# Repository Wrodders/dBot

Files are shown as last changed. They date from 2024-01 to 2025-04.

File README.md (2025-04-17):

# Two Wheel Self Balancing Mobile Robot

Final Year Capstone Mechatronics Project. 
Designed to be a cost effective platform for research and development of autonomous 
mobile robotics. The non linear and unstable dynamics of the Two Wheel Self Balancing Mobile Robot (TWSBMR)
make it a challenging platform for control and navigation.

Low Level motor control implemented on STM32F411RE microcontroller, using LibOpenCM3.
High Level Monocular Navigation uses RaspberryPi 5 with the Pi Camera V3.
[ComsTerm](https://github.com/Wrodders/ComsTerm) used as engineering UI. 

## Design
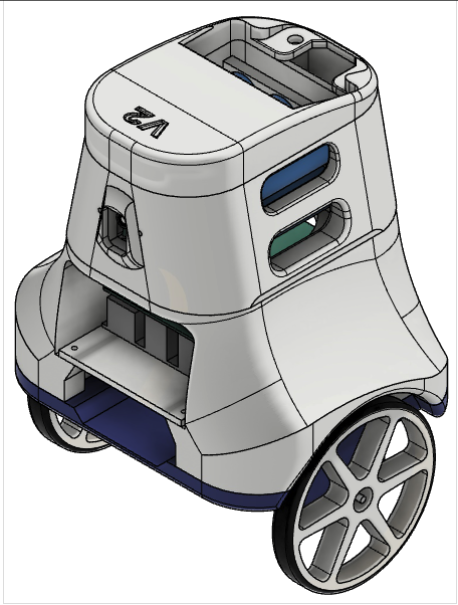
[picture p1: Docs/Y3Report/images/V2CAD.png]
botISO


The project was built around milestones of autonomy:

* Stabilization
* Positional Control
* Teleoperation
* Path Following 
* Path Recovery 
* Track Racing

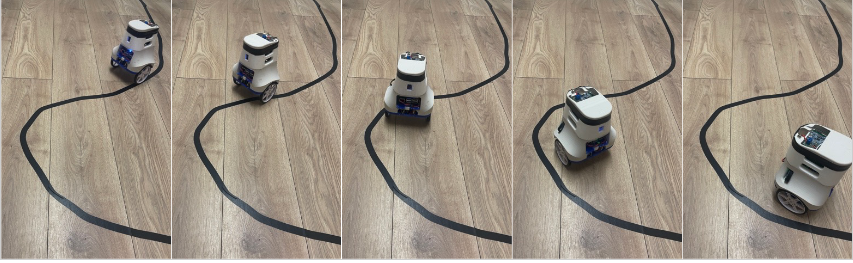
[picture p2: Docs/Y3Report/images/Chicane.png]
CurveSequence


Cascaded_Controller

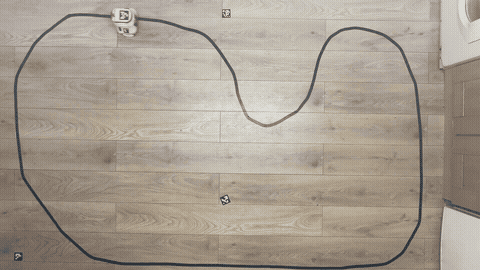
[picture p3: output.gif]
Video


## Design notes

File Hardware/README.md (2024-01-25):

# STM32 Black Pill Connection Diagram

```mermaid
graph TB
  subgraph STM32F401
    USART2 -->|PA2/3| Debug/Prog
    USART1 -->|PB6/7| Bluetooth
    TIMER3 -->|PA6/7 PB0/1| PWM
    TIMER1 -->|PA8/9/10/11| Encoder
    I2C1 --> |PB8/9| MPU6050
  end
```

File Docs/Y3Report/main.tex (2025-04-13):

%%%%%%%%%%%%%%%%%% USAGE INSTRUCTIONS %%%%%%%%%%%%%%%%%%
% - Compile using LuaLaTeX and biber, unless there is a particular reason not to. Do not use the older LaTex/PDFLaTeX or BibTeX. (The fonts won't work correctly.)
% - Font and the report 'year' must be specified when all \documentclass or the template won't work correctly. (There's no error checking/default cases!)
% - For best performance save images/graphics as PDF files, not as png/jpg/eps. This makes no difference to how images are inserted using \includegraphics.
% - As many further packages as wanted can be loaded. Below are just an example set. Note that template itself loads a number of packages, including hyperref.
% - References are handed using biblatex.
% - Link to the presentation of theses policy: https://documents.manchester.ac.uk/DocuInfo.aspx?DocID=2863

%%%%%%%%%%%%%%%%%% META DATA SETUP %%%%%%%%%%%%%%%%%%
% This is where the document title and author are set. Other details for the title page are set later
% Note that if/when you edit these you may need to 'Recompile from scratch' to get the changes to display in the PDF. (In Overleaf, select the down arrow to the right of the 'Recompile' button)

    \begin{filecontents*}{\jobname.xmpdata}
        \Language{en-GB}
        \Copyrighted{True}
        % More meta-data fielda can be added here if wanted, see https://ctan.org/pkg/pdfx?lang=en for fields
    \end{filecontents*}

    %%%%%%%%%%%%%%%%%% DOCUMENT SETUP %%%%%%%%%%%%%%%%%%
    \documentclass[12pt]{uom_eee_dissertation_casson} 
    %%%%%%%%%%%%%%%%%% PACKAGES AND COMMANDS %%%%%%%%%%%%%%%%%%
    % Packages
    \usepackage{graphicx,psfrag,color} % for postscript graphics files
        \graphicspath{ {./images/} }   % where to look for images
    \usepackage{amsmath}               % assumes amsmath package installed
        \allowdisplaybreaks[1]         % allow eqnarrays to break across pages
    \usepackage{amssymb}               % assumes amsmath package installed 
    \usepackage{url}                   % format hyperlinks correctly
    \usepackage{rotating}              % allow portrait figures and tables
    \usepackage{multirow}              % allows merging of rows in tables
    \usepackage{lscape}                % allows pages to be typeset in landscape mode
    \usepackage{tabularx}              % allows fixed width tables
    \usepackage{verbatim}              % enhanced version of built-in verbatim environment
    \usepackage{footnote}              % allows more control over footnote environments
    \usepackage{float}                 % allows H option on floats to force here placement
    \usepackage{booktabs}              % improve table line spacing
    \usepackage{lipsum}                % for adding dummy text here
    \usepackage[base]{babel}           % for proper hypthenation in lipsum sections
    \usepackage{subcaption}            % for multiple sub-figures in a single float
    % Add your packages here
    %\usepackage{pdfcomment}            % for alt text for accessibility
    \usepackage{booktabs}              % for better looking tables
    \usepackage[ruled,vlined]{algorithm2e}

    % Then to add images use:
    % \pdftooltip{\includegraphics[width=0.5\textwidth]{image.pdf}}{Alt-text here}
    % This makes the text in the image non-select-able though (assuming it's a vector file)
    
    % Custom commands
    \newcommand{\degree}{\ensuremath{^\circ}}
    \newcommand{\sus}[1]{$^{\mbox{\scriptsize #1}}$} % superscript in text (e.g. 1st)
    \newcommand{\sub}[1]{$_{\mbox{\scriptsize #1}}$} % subscript in text
    \newcommand{\sect}[1]{Section~\ref{#1}}
    \newcommand{\fig}[1]{Fig.~\ref{#1}}
    \newcommand{\tab}[1]{Table~\ref{#1}}
    \newcommand{\equ}[1]{(\ref{#1})}
    \newcommand{\appx}[1]{Appendix~\ref{#1}}
    %%%%%%%%%%%%%%%%%% REFERENCES SETUP %%%%%%%%%%%%%%%%%%
    % Setup your references here. Change the reference style here if wanted
    \usepackage[style=ieee,backend=biber,backref=true,hyperref=auto]{biblatex}
    % Note backref=true adds a page number (and hyperlink) to each reference so you can easily go back from the references to the main document. You may prefer backref=false if you need to stick strictly to a given reference style
    % Fixes which can't be applied in the .cls file
    \DefineBibliographyStrings{english}{backrefpage = {cited on p\adddot},  backrefpages = {cited on pp\adddot}}
    %  \renewcommand*{\bibfont}{\large}
    % Add more .bib files here if wanted
    \addbibresource{references.bib }
    
    %%%%%%%%%%%%%%%%%% START DOCUMENT %%%%%%%%%%%%%%%%%%

    \begin{document}
    \makeatletter
    \title{Design of a Two Wheel Self Balancing Line Racing Platform} % title of your thesis
    \author{Winston Scott}
    \studentid{107067151}
    \makeatother                                               
    \maketitle

    %%%%%%%%%%%%%%%%%% LISTS OF CONTENT %%%%%%%%%%%%%%%%%%
    \wordcount{9300}		                    % use \wordcount{} to set the count, \thewordcount to print in the text
    \uomtoc
    \begin{uomterms}
        \textbf{TWSB}:Two Wheel Self Balancing \\
        \textbf{DDMR}:Differential Drive Mobile Robot \\
        \textbf{LQR}:Linear Quadratic Regulator \\
        \textbf{MEMS}:Micro-Electro-Mechanical Systems \\
        \textbf{MPC}:Model Predictive Control \\
        \textbf{MCU}:Microcontroler Unit \\
        \textbf{RPC}:Remote Procedure Call \\
        \textbf{IMU}:Inertial Measurement Unit \\
        \textbf{ppr}:Pulses Per Revolution \\
        \textbf{KF}:Kalman Filter \\
    \end{uomterms}

    \uomdeclarations

    %%%%%%%%%%%%%%%%%% ABSTRACT %%%%%%%%%%%%%%%%%%
    \begin{abstract} % put abstract here. Limit is 1 page.
        The highly dynamic Two Wheel Self Balancing Robot 
        (TWSB) has a large exploration space for developing high-level 
        control strategies. 
        This report presents the design decisions and algorithms developed for
        an autonomous line-racing TWSB robot utilizing a monocular vision system with low-cost hardware. 
        System identification techniques are used to explore
        cascaded PID control strategies for the TWSB system.
        A trajectory generation algorithm is proposed based on drivability, confidence, 
        and prominence of the detected line from a camera used as an intensity sensor. 
        The performance of the system is shown to be robust to different race tracks with
        surface texture variation, lighting conditions, high-speed straights, and tight curves. 
  \end{abstract}%
  \clearpage

  %%%%%%%%%%%%%%%%%% SECTION 1 %%%%%%%%%%%%%%%%%%
    \section{Introduction}
    The Two Wheel Self Balancing (TWSB) platform is a nonlinear, underactuated system which is only dynamically stable.
    Compared to the differential drive mobile platform (DDMR), the TWSB requires active control effort
    to maintain its upright posture while in motion and when stationary.
    Substantial research has been conducted on the similarly unstable 1-DOF inverted pendulum on a cart 
    as a benchmark for control techniques \cite{boubaker2013inverted}. 
    The TWSB robot serves as a cost-effective platform for research and education in complex control 
    strategies less commonly applied to statically stable wheeled robots \cite{educationPlatform}.

    Controlling this unstable degree of freedom expands the range of autonomous behaviors that 
    can be explored \cite{RoboLimbo} \cite{jeong2008wheeled} \cite{Browning2004TurningSI}. 
    These behaviors necessitate a hierarchical design in the system's architecture,
    where planning and navigation algorithms though linked, are decoupled by levels of abstraction 
    from the low-level stability control and even lower-level motor control. This paper explores 
    the design tradeoffs at each of these levels, and the challenges with developing a robust system 
    capable of autonomous navigation in a variety of indoor environments using a monocular camera.

    A notable work on the TWSB system is \cite{grasser2002joe} which designed a TWSB robot capable of disturbance
    rejection and static pose control on an inclined plane. This was implemented using an FPGA-based DSP system.
    The controller design decouples the balancing and steering torques in state space through the Linear Quadratic Regulator (LQR), 
    allowing the platform can turn about its center effectively. This is a behavior that is fundamental to differential drive robots, 
    and accomplishing this allows for the TWSB to be navigated similarly.
    An early challenge in the navigation of the TWSB system identified by \cite{SelfContainedMobileTWSB} is the sensor 
    system used for state estimation. The proposed solution uses a gyroscope as an angular rate sensor, though it 
    was noted to suffer from drift. Accounting for this drift as a linear function over time, the authors were able to 
    stabilize the system and teleoperated it over short distances. 

    Advances in the cost-to-performance of embedded systems and micro-electromechanical sensors (MEMS) \cite{MEMS} 
    have allowed \cite{juang2013design} \cite{Velazquez2016VelocityAM} to control the TWSB system 
    using low-powered microcontrolers. This then poses the question of how to expand the capabilities 
    of the TWSB system beyond teleoperation by utilizing modern embedded computers for high-level autonomy. 
    Recent research has also applied reinforcement learning to mobile robotic systems \cite{kober2013reinforcement}.
    Neural networks are proposed as nonlinear function approximations to model the system's response. 
    These methods demonstrate robustness to un-modeled or neglected dynamics \cite{guo2021optimal}.

    In mobile robotics, the ability to navigate requires perception. LIDARs are commonly used, as  
    the depth of information they capture naturally lends itself to path-planning algorithms.
    Another commonly used multimodal sensor is the CMOS camera, which measures light intensity at each pixel. 
    When paired in stereo, it can efficiently infer depth, providing a suitable alternative to the point 
    clouds generated by LIDAR. Although monocular vision systems are desirable due to their simplicity, 
    the redundancy of stereo vision is beneficial in safety-critical applications.
    Both these sensors provide rich environmental data that can be leveraged to develop long-term path-planning algorithms \cite{gonzalez2015review}.

    This paper is split into 2 parts, the first part focuses on the design of the TWSB system, and the second part
    develops a vision-based line-following algorithm, geared towards racing applications. By exploring 
    the performance of the TWSB at its handling limits, this project tests the viability of the designed robot
    as a platform for further research on wheel robotic navigation. 

    Autonomy is achieved using a hierarchical cascaded PID feedback controller. This aims 
    to regulate the pitch angle maintaining balance when controlling the robot's linear velocity. 
    Once these requirements are met, the robot can be teleoperated intuitively via a 
    smartphone-based web interface. The remainder of this paper focuses on incorporating 
    multimodal sensor data from the camera to develop line-racing algorithms.
    The robot algorithmically infers and follows an unknown line using a monocular camera. 
    A hardware-in-the-loop software architecture is implemented, enabling real-time telemetry data and control 
    commands to be exchanged between the robot and a remote computer, but all computations are performed onboard. 
    Visualization of this telemetry data provides a straightforward means of validating the robot's performance.

  %%%%%%%%%%%%%%%%%% SECTION 2 %%%%%%%%%%%%%%%%%%
    \section{Mathematical Modeling} % edit section heading as appropriate
    In this report, the TWSB decomposed into 2 commonly studied 2DOF subsystems, described by Fig.\ref{fig:2DOF}, and their behavior is analyzed
    separately.
    Effective control and planning algorithms for such platforms require the designer to obtain a mathematical model describing the behavior
    of the robot.  
    For the TWSB system, these models are commonly obtained by a linear approximation of the dynamics similar to 
    of the classic inverted pendulum \cite{AdvancedWIP}.
        \begin{figure}[h]
            \centering
            \begin{subfigure}[b]{0.4\textwidth}
                
                \caption{Differential Drive Mobile Robot}
                \label{fig:DDMR}
            \end{subfigure}
            \hfill
            \begin{subfigure}[b]{0.4\textwidth}
                
                \caption{Wheeled Inverted Pendulum}
                \label{fig:WIP}
            \end{subfigure}        
            \caption{Robot subsystems}
            \label{fig:2DOF}
        \end{figure}

        \subsubsection{Differential Drive Mobile Robot}
    Wheeled mobile robots are typically restricted to navigation in the 2D Cartesian plane. For small robots 
    this configuration, motion models are often simplified by discounting the nonlinear dynamics of friction and 
    the inertial forces arising from acceleration in the $X'$ direction are negligible \cite{KinematicWheeled}. 

    The DDMR's nonlinear kinematics are obtained from Fig.\ref{fig:DDMR} describe point $G=(x_g,y_g)$ as the position of 
    the robot in the global frame.
        \begin{equation}
            \begin{bmatrix}
                \dot x_g \\
                \dot y_g \\
                \dot \psi
            \end{bmatrix}
    =
            \begin{bmatrix}
                \cos(\psi) & 0 \\
                \sin(\psi) & 0 \\
                0 & 1
            \end{bmatrix}
            \begin{bmatrix}
    v_g \\
                \omega_g
            \end{bmatrix}
            \label{eq:DDMRGlobal}
        \end{equation}

    Where the angular velocity $\omega_g$ and linear velocity $v_g$ are the control 
    inputs to the system. 

    The motion of the DDMR is bounded by its non-holonomic constraints, 
    preventing lateral movement along the $Y'$ axis. 
    Under the pure rolling assumption, the wheels do not slip, and the robot's kinematics 
    are governed by the wheel radius $r$ and wheelbase $d$. These parameters define 
    the mapping between the left and right wheel velocities, $\omega_L$ and $\omega_R$, 
    and the global velocities $v_g$ and $\omega_g$, by:
        \begin{equation}
            \begin{bmatrix}
    v_g \\
                \omega_g
            \end{bmatrix}
    =
            \begin{bmatrix}
                \frac{r}{2} & \frac{r}{2} \\
                \frac{r}{d} & -\frac{r}{d}
            \end{bmatrix}
            \begin{bmatrix}
                \omega_L \\
                \omega_R
            \end{bmatrix}
            \label{eq:DDMR}
        \end{equation}

        \subsection{DC Motor Model}    
    The robot is driven by two DC motors, through planetary gearboxes, as shown in Fig.~\ref{fig:DCMotor}.
    When a voltage $V_a$ is applied, the DC motor generates a torque, $\tau$, 
    proportional to the armature current, $i_a$.
    According to Lenz's law, the back electromotive force (emf), $e_a(t)$, 
    opposes the applied voltage. These relations are given by:
        \begin{subequations}
            \begin{align}
                \tau &= K_t i_a \\
    e_a &= K_e \dot{\phi}_r
            \end{align}
        \end{subequations}
    where $\dot{\phi}_r$ represents the rotor's angular velocity. The torque 
    and back emf constants are denoted as $K_t$ and $K_e$, respectively.
        \begin{figure}[H]
            \centering
                
            \caption{Gearbox DC Motor Model Diagram}
            \label{fig:DCMotor}
        \end{figure}
    In small motors, since $L_a \ll R_a$, the electrical dynamics can be approximated as:
        \begin{equation}
    i_a (t) = \frac{V_a (t) - K_e \dot{\phi}_r (t)}{R_a}
        \end{equation}

    The rotor torque, $\tau_r$, is transmitted through the gearbox, which 
    reduces the angular velocity of the wheel, $\dot{\phi}_w$, by the gear ratio $n = \frac{N_2}{N_1}$. 
    Assuming the gearbox is lossless the wheel torque, $\tau_w$, is given by:
        \begin{equation}
                \tau_w = n\tau_r
        \end{equation}
    where $N_1$ and $N_2$ are the number of teeth on the input and output gears, respectively.
    The rotor's inertia $J_r$ and the drive train damping, $B_r$ and $B_g$, are also considered negligible.
    By summing the torques of the rotor and gearbox subsystems, the output torque is given as:
        \begin{equation}
            \tau_w = - J_g \ddot{\phi}_w - \dot{\phi}_w \left( \frac{K_t K_e}{R_a} n^2 \right) + \frac{n K_t V_a}{R_a}
            \label{eq:DCMotorTorque}
        \end{equation}
    where $J_g$ represents the gearbox's inertia and $B_g$ its damping coefficient.

        \subsection{Wheeled Inverted Pendulum}
    The wheel inverted pendulum (WIP), is similar to the classic inverted pendulum on a cart. 
    The WIP is composed of 2 rigid bodies, the body and the chassis connected by a revolute joint, 
    at the center of mass of the wheel as shown in Fig.\ref{fig:WIP}. 
    The center of mass of the body, $B=(x_b,z_b)$, 
    is located at a distance $L$ from the wheel's axel, displaced at some pitch angle $\theta$ with 
    the vertical axis $Z$. The body is assumed to be a point mass $M_b$ with a moment of inertia $J_b$ 
    about the axis of rotation. 
        
    The system of equations governing the time evolution of the WIP are well known.
        \cite{frankovsky2017modeling} \cite{ModelingWIPLagrange}.
    This paper uses the 2DOF state space model as obtained by \cite{Velazquez2016VelocityAM} since it describes 
    the hardware of a similar configuration to the TWSB designed in this project. 
    Incorporating the torque produced by each actuator, eq(\ref{eq:DCMotorTorque}),
    and reiterating the no-slip condition 
        \begin{equation}
            \phi_w = \frac{x}{r}
        \end{equation}
    the model is re-expressed in the notation of this report as 
        \begin{equation}
            \begin{bmatrix}
            \dot{x} \\
            \ddot{x} \\
            \dot{\theta} \\
            \ddot{\theta} 
            \end{bmatrix} =
            \begin{bmatrix}
            0 & 0 & 0 & 0\\
            0 & \frac{2n^2 K_t K_e }{r^2 R_a W_1 } & \frac{-M_b^2 L^2 g}{W_1 \left(J_b +M_b L^2 \right)} & 0\\
            0 & 0 & 0 & 1\\
            0 & \frac{2n^2 K_t K_e }{r^2 R_a W_2 } & \frac{-M_b^2 L^2 g}{W_2 \left(\left(J_b +M_b L^2 \right)+W_1 g\right)} & 0
            \end{bmatrix}
            \begin{bmatrix}
    x\\
            \dot{x} \\
            \theta \\
            \dot{\theta} 
            \end{bmatrix} +
            \begin{bmatrix}
            0\\
            -2n\frac{K_t }{W_1 R_a r}\\
            0\\
            -2n\;\frac{K_t }{W_2 R_a r}
            \end{bmatrix}
    V_a
        \label{eq:2DOF}
        \end{equation}

    with 
        \[
    W_1 = 2\left(\frac{-n^2 J_g + J_w }{r^2 } - M_w \right) - M_b + \frac{M_b^2 L^2 }{J_b + M_b L^2 }
        \]
        \[
    W_2 = W_1 \left(\frac{J_b }{M_b L} + L\right)
        \]

    Where $M_w$ is the mass of the wheel, $J_w$ is the moment of inertia of the wheel.
    \pagebreak{}

    \section{System Design}
        The robot must be designed to approximate the wheel-inverted pendulum system, many authors 
        construct demonstrators supporting a mass with a rectangular structure built out of lead screws. 
        This allows for experimentation with the system's center of mass and is simple to construct. 
        A proof of concept system was developed in this manner, however, the exposed electronics were 
        susceptible to damage during tuning of the balance and navigation algorithms.

        As such the TWSB body is 3D printed out of PLA plastic in 3 parts for minimal assembly.
        The battery pack is quickly swappable and both it and the electronics sub-assembly 
        are soft-mounted in a roll cage-like housing for protection against impacts. 
        The wheels are protected by wheel arches which serve to minimize risk of damage to the motor shaft on wheel impacts. 
        Wiring harnesses are routed through channels to minimize snagging and disconnection from vibrations.
        
        \begin{figure}[H]
            
            \caption{CAD Drawing of the TWSB system dimensions in mm}
            \label{fig:CAD}
        \end{figure}

        Two brushed DC motors are powered by an H-Bridge IC, DRV7783. 
        The STM32F411RE Microcontroller Unit (MCU) is used to control the 
        motors and monitor the 6 6-axis inertial Measurement Unit (IMU) over I2C. It communicates with the 
        Raspberry Pi 5 over UART via a custom ASCII protocol discussed in section 3.1. 
        The system is powered by a 12V nominal Li-ion Battery pack. A USB-C CC-CV charger is used for quick 
        and accessible recharging, critical for mobile robotics applications. 
        Battery voltage is monitored by the MCU and the pack is protected by a BMS.
        A simple circuit adapted from \cite{chu2008designing} is used to safely load share between the battery pack and the charger.

        \subsection{Software Architecture}
        The modern standard for robotics software is the Robot Operating System 2 (ROS2) \cite{Macenski2022RobotOS}. 
        It is composed of several highly configurable applications that are designed to be managed in a distributed system.
        Distributed systems are beneficial in robotics development as they functionally decouple the software components, 
        enabling robust failure recovery and ease of integrating new features. This concept is useful for this project as 
        the core control and vision systems are developed in parallel. The controls, logs, and error recovery systems mandate 
        high availability compared to user interfaces such as the remote control web app. 
        Whilst this is a powerful tool, it is deemed too complex to learn to meet the project deadline.
        Nevertheless, some core concepts are used such as sharing state by message passing between components, 
        and dynamic parameter configuration to improve testing and data collection. The ZeroMQ middleware is used for 
        timestamped signal stream communication between the computational nodes. 
       
        The software, written in C++, is managed by Systemd as a service. 
        Self-diagnosis routines are used for resource monitoring and auto-recovery. 
        Programs operate on runtime parameters through Remote Procedure Calls (RPC) 
        interface using a GET-SET pattern. This reduces the 
        compile flash debug iteration time. A GStreamer pipeline sets up a video 
        server accessible over LAN. OpenCV is used for optimized image processing.
             
        The firmware is implemented in C using register definitions from the 
        libopencm3 project \cite{BeginningSTM32} as an exercise in low-level programming. 
        No dynamic memory allocation is used.
        The resultant binary is 19KB with 892B of RAM used.
              
        The data-acquisition system obtains a timestamped sample of the 
        telemetry values transmitted by the MCU through a serial link, which implements the
        RPC interface over uart at 230400 baud, 
        it executes commands and publishes telemetry packets at 100Hz.
        Parsing the UART IO buffer can result in non-uniformly sampled data as it
        is constrained by the OS scheduler, thus an event-driven system is used to 
        minimize CPU overhead.
               \subsubsection{Parameters }
        The system parameters are given in Table \ref(tab:SysParams). 
        The mass of the sub-components is obtained by weighing,
        and estimates of the 3D printed parts' mass are given by the slicer software. 
        The CAD files are used in MATLAB's Multibody Simulink environment, which 
        computes the center of mass and the moments of inertia can subsequently be estimated.
        The Motor parameters are estimated through the system identification experiments discussed in section 3.2.
                    
        \begin{table} [H]
            \centering
            \begin{tabular}{|c|c|c|c|}
                \hline
                Parameter & Value & Units & Description \\
                \hline
                $M_b$ & 0.8 & kg & Mass of the body \\
                $L$ & 0.08135 & m & Height of COM above wheel axel \\
                $J_b$ & 0.0071& kgm$^2$ & Moment of inertia of the body \\
                $r$ & 0.04 & m & Radius of the wheel \\
                $M_w$ & 0.09 & kg & Mass of wheel assembly \\
                $J_w$ & 0.000072 & kgm$^2$ & Moment of inertia of the wheel \\
                $d$ & 0.132 & m & Wheel base \\
                $R_a$ & 1.5 & $\Omega$ & Resistance of the motor \\
                $K_t$ & 0.24 & Nm/A & Torque constant of the motor \\
                $K_e$ & 0.18 & V/rad/s & Back EMF constant of the motor \\
                $n$ & 20 & - & Gear ratio \\
                $J_g$ & 0.0003 & kgm$^2$ & Moment of inertia of the gearbox \\
                \hline
            \end{tabular}
            \caption{System Parameters}
            \label{tab:SysParams}
        \end{table}

        \subsection{System Identification}
        A set of experiments are conducted to evaluate the transfer function of the motors.

        \begin{table}[H]
            \centering
                \begin{tabular}{|r|c|c|c|c|c|c|}
                    \hline 
                    Gear Ratio & Rated Torque & Rated Speed  & Rated Current & Stall Current & Stall Torque \\
                    \hline
                     1:20  & 0.39 Nm & 600 rpm & 500 mA & 2 A & 0.15 Nm/Kg \\
                    \hline
                \end{tabular}
                \caption{Manufacturer Provided Motor Parameters}
        \end{table}

        A telemetry and analysis software system developed in Python. It is used as 
        test bench  setup shown in Fig.\ref{fig:SysIDSetUp}, a series of reference 
        ramp, step, sine, and chirp inputs are applied to each motor.

        The test suite contains a time-series signal generator, with preview and playback functionality.
        The system logs and messages are displayed in a terminal window, and the user can fully configure 
        each node's runtime parameters remotely over a network connection, utilizing the RPC ASCII protocol.
        A line plotter is configured by JSON to display any number of signals the robot may produce.
        This architecture allows for repeatability in obtaining robot data, something 
        is is a challenge in mobile robotics.
        
        \begin{figure}[H]
            \centering
            
            \caption{System Identification Testbench Setup}
            \label{fig:SysIDSetUp}
        \end{figure}
      
        This software system is also utilized for heuristic tuning of the control
        and vision systems. The program can visualize control signal streams in soft real-time 
        and provides a useful insight into the effects of the control system on the plant.

        \begin{figure}[H]
            \centering
            \begin{subfigure}[b]{0.45\textwidth}
            
            \caption{Open Loop Step Response}
            \label{fig:openstep}
            \end{subfigure}
            \hfill
            \begin{subfigure}[b]{0.45\textwidth}
            
            \caption{Open Loop Sine Response}
            \label{fig:opensine}
            \end{subfigure}
            \caption{Open Loop no Load Speed Voltage Experiments}
            \label{fig:openloop}
        \end{figure}

        From these experiments, it is clear that the motor has significant deadzones, 
        and the input-output relationship is nonlinear at low armature voltages. 
        The maximum no-load speed within the manufacturer's operating range is found to be 8 rotations per second.
        To increase control authority, the motors are powered by 12V, with the armature voltage modulated by 
        the duty cycle of the PWM signal. The DRV7783 Integrates current sensing and over-current protection,
        used to limit the current to the motors to 1.5A.
              
        For stationary balancing of the TWSB robot
        the actuators are required to operate mostly in a sinusoidal fashion, 
        similar to Fig.\ref{fig:opensine}, to regulate the pitch angle of the body.
        Considering this a closed-loop controller is developed in section 5.1 to regulate the motor speed,
        and maintain the device in its operating region. 
       
           \section{State Estimation}
        Information about the TWSB system may be obtained from 2 kinds of sources; 
        mathematical models models as in eq(\ref{eq:2DOF}) which can describe the time evolution of the chosen system variables, 
        and sensors that convert energy arising from a physical property into information. Both of these sources 
        are approximations of the true state. The process of combining multiple sources of information is termed sensor fusion.
        This section evaluates the available methods employed using \textit{proprioceptive} sensors.
           \subsection{Sensors Overview}
        For the TWSB system in eq(\ref{eq:2DOF}) its state variables $\theta$ and $\dot x_b$ can be measured through the onboard IMU 
        and the wheel encoders respectively. 
                   
        The motors incorporate a low-cost 12 pulses per revolution (PPR) incremental encoder on the rotor shaft. 
        Further resolution is easily obtained by using the MCU's quadrature 
        peripheral to increment, or decrement, a counter based on the phase transitions.
        Considering the gearbox ratio $n=20$, an effective resolution of 960 PPR is attained.
        The rotational speed of the wheel is computed by sampling the change in the pulse counts
        over a sample period $\Delta t$. Thus the error in the velocity estimate, 
        is inversely proportional sample period, resulting in larger errors at low speeds.
        Yet, it is observed that more significant sources of error arise from the mechanical backlash in the gearbox.
        The sample time is set to 2 ms, and a low-pass filter is given by the infinite recursive relation as
        \begin{equation}
            y_k = \alpha x_k + (1-\alpha)y_{k-1}
            \label{eq:lpf}
        \end{equation}
        exponentially attenuates sudden deviations in the velocity estimate by selecting $\alpha = 0.95$.
       
        Using this velocity estimate in the model of the DDMR from eq(\ref{eq:DDMRGlobal}) to obtain the
        position of the robot in the cartesian plane as ($x_g,y_g$) is known as odometry.
        There are various sources of errors in 
        this process, arising from assembly imperfections and conditions in 
        the environment which may break the constraints assumed in the kinematics of the DDMR.
                   
        These conditions become significant in the case of the TWSB system as crashes, or bumps, result in large 
        and unbounded error accumulation. In the case of crashes, the robot is subsequently stationary 
        and its state is reset. However, in the case of bumps, where the robot can recover, corrective 
        action is required to mitigate this. Assuming a sufficiently accurate wheel encoder, a simple method is 
        implemented based on \cite{Gyrodometry}, only correcting 
        the odometry when such events are detected.  
        This leads to the decision that other forms of systematic odometry errors have to be 
        either disregarded in the short term or corrected by landmark methods by $exteroceptive$ sensors. 
       
        The IMU is a 6-axis MEMS sensor \cite{ComplimentaryKalman} which measures the local linear acceleration 
        and angular velocity.
        The 3D acceleration, $\vec{a}$, is used to obtain an 
        estimate of the pitch angle as $\hat{\theta} = \mathrm{atan2}\left(-a_x ,a_z \right)$
       
        The variance of this $\hat{\theta}$ is small when the system is at rest but grows larger when subject to vibration from the motors
        as shown by the experiment in Fig.\ref{fig:accelNoise} where the TWSB is placed horizontally at rest and motor control commands are issued. 
        \begin{figure}[H]
            \centering
            \begin{subfigure}[b]{0.5\textwidth}

                
                \caption{Accelerometer is sensitive to motor vibrations}
                \label{fig:accelRaw}
                
            \end{subfigure}
            \hfill
            \begin{subfigure}[b]{0.45\textwidth}
                
                \caption{Wide Variance on pitch estimate at rest}
                \label{fig:pitchNoise}
            \end{subfigure}
            \caption{Accelerometer Noise}   
            \label{fig:accelNoise}
        \end{figure}

        From \ref{fig:pitchNoise} it can be seen that the IMU is not mounted perfectly orthogonal to the body frame. 
        \begin{table}[H]
            \centering
            \begin{tabular}{c c c} 
                \toprule
                $a_{x_0}$ & $a_{y_0}$ & $a_{z_0}$ \\
                \midrule
                0.036453 & -0.0021066 & 0.133658 \\
                \bottomrule

            \end{tabular}
            \caption{Accelerometer Mounting Offset (m/s$^{2}$)}
            \label{tab:accelOffset}
        \end{table}
        This systematic error is removed by utilizing calibrated values in Table \ref{tab:accelOffset}.
        \subsection{Kalman Filter}
        The Kalman Filter (KF) and its variants  are widely used in robotics to fuse 
        complementary sources of information \cite{Thrun2005ProbabilisticRobotics} \cite{perez2023quadcopter} \cite{Moore2014AGE}.
        Even though the state transition model of the TWSB robot is non-linear \cite{ooi2003balancing} 
        developed self-balancing platforms capable of restricting oscillations about the 
        operating point to $±1$ degree. This is one order of magnitude than the worst-case linearization pitch limit of $±10$ degrees.
        Beyond this, the small angle approximation is no longer valid, and the system is not locally linear. As such it is determined 
        that if the controller is able to regulate the pitch to within this range, then the optimum linear estimator known as the Kalman Filter is suitable.

        The Kalman Filter is a 2-stage recursive estimator which uses the system model to predict the state of the system,
        and then corrects this prediction using the measurements from the sensors. The notion of a prediction and correction 
        stems from Bayesian statistics, where signals are modeled as random variables with a probability distribution.
        The Kalman Filter is applicable to linear systems, and as such the random variables are assumed to be normally distributed. 
        Considering a linear stochastic system of the form:

        \begin{equation}
            x_t = A_t x_{t-1} + B_t u_t + \epsilon_t
        \end{equation}

        where $\epsilon_t$ is a noise term with zero mean and covariance $Q_t$. The Kalman Filter is concerned with 
        updating its posterior belief in the true state of \textit{bel}$(x_t)$ with some weighted sum of the 
        information from the prior belief \textit{$\bar{\text{bel}}(x_t)$}, the current measurement $z_t$, and the evolution of 
        the model of the system through the control action $u_t$.

        At each time step $t$, the TWSB system obtains new measurements from its sensors, which are related to the state space by:

        \begin{equation}
            z_t = C_t x_t + \delta_t
        \end{equation}

        where $\delta_t$ is a noise term with zero mean and covariance $R_t$.  
        Often noise variables of this kind are denoted as part of the $N(0, R_t)$ group of random variables.
        The matrix $C_t$ maps the measurements to the state space as a linear transformation.

        Before the measurement can be used, the Kalman Filter must first obtain an estimate of the state given the 
        prior belief and the control action. This is termed the prediction stage, where the current mean, given the prior mean, 
        is predicted through applying the current control action to the system model. This prediction increases the uncertainty of the belief through the 
        process noise, which is a random variable given as $N(0, Q_t)$. This process noise is assumed to be independent from the measurement noise.
        The prediction step is given by the equations:

        \begin{equation}
            \mu_{t|t-1} = A_t \mu_{t-1|t-1} + B_t u_t
        \end{equation}
        \begin{equation}
            P_{t|t-1} = A_t P_{t-1|t-1} A_t^T + Q_t
        \end{equation}

        By the linearity of Gaussian distributions, incorporating the measurement will reduce the uncertainty in the posterior belief. 
        This is done through the Kalman Gain matrix as:

        \begin{equation}
            K_t = P_{t|t-1} C_t^T (C_t P_{t|t-1} C_t^T + R_t)^{-1}
        \end{equation}
        \begin{equation}
            \mu_{t|t} = \mu_{t|t-1} + K_t (z_t - C_t \mu_{t|t-1})
        \end{equation}
        \begin{equation}
            P_{t|t} = (I - K_t C_t) P_{t|t-1}
        \end{equation}

        The state transition model used by the KF can be chosen to model the TWSB system eq(\ref{eq:2DOF}) as a step towards 
        full state feedback, or solely based the dynamics of the IMU.
            
        The MPU6050 6-Axis IMU can be used to  estimate the pitch through the 
        gyroscope measurement $\vec\omega_{gyro}$, which due to its mass spring construction, even if miniutrazizred, suffers from a drift noise term. 

        \begin{equation}
            \vec\omega_{gyro} = \omega + b_g + n_g
        \end{equation}

        and the accelerometer measurement \ensuremath{\vec{\alpha}_{accel}} is from as 
        
        \begin{equation}
            \vec{\alpha}_{accel} = \alpha - g + b_a + n_a
        \end{equation}
        Where the external acceleration arising form linear motion is given as $\alpha$, accelerometers bias by $b_a$ and noise by $n_a$. 

        A Kalman Estimator is developed to fuse the gyroscope and accelerometer measurements, using the model of the IMU obtained similar to \cite{ComplimentaryKalman}.
        This is implemented on the microcontroler at 1Khz.  

        \begin{figure}[H]
            \centering
            
            \caption{Sensor Fusion of accelerometer and gyroscope}
            \label{fig:SensorFusion}
        \end{figure}
             
        Fig.\ref{fig:SensorFusion} shows that the Kalman Filter's produces a smooth estimate of the pitch angle
        under conditions of the experiment in Fig.\ref{fig:accelNoise}. 
        \pagebreak{}

    \section{Control System}
        Autonomy in mobile robotics is commonly a hierarchical problem composed of high-level path planning, 
        or task allocation, and low-level control of the actuators.  
        Successful implementations must design solutions to both of these problems in a complementary manner in order 
        to achieve the desired system behavior, of tracking the planned configurations.
                
        For the TWSB robot, behavior can be described by two main goals, static balancing and navigation.
        These two behaviors are inherently coupled due to the system's underactuated design. Hence, the 
        magnitude of the feedback required for sufficiently fast stabilization leads to significant chatter or oscillations 
        in the control signal.
    
        Gain scheduling is suggested by \cite{refvem2019design}
        as a way to operate the system in these two different modes. A similarly underactuated system is controlled via this 
        method by \cite{wanggain}. Notably, in these cases care must be taken to ensure 
        that discontinuities in the control signal at the point of switching do not cause instability \cite{hespanha2002switching}.
        Determining the switching schedule is a nontrivial problem, often mandating experimental validation-dependent 
        on the systems parameters, \cite{RoboLimbo} utilizes advanced nonlinear strategies to determine these
        boundary conditions.
    
        The tracking performance of reactive control strategies is often bounded by the control effort 
        demanded within the bandwidth of the actuators. Typically in feedback systems, a saturation function 
        is utilized on the reference to enforce safe operation. This discontinuity breaks the linearity of the 
        controller often leading to oscillations, and care must be taken to avoid such limit cycles.
                
        The PID regulator is an attractive choice for many systems, as by nature of negative feedback it does not 
        require an explicit model of the plant to operate. The process variable is typically a direct measurement 
        obtained by a sensor, and the control law $u_k$ is computed reactively to an error signal at each timestamp $k$.
        Oftentimes, intuition about the signal's physical units is sufficient to tune the feedback gains adequately. 
        However, performance validation in the model-free case must be evaluated at runtime, this may prove to be 
        challenging or destructive in cases of unstable or safety-critical systems. 
            
        Heuristic methods such as Ziegler-Nichols formulate approaches to black-box tuning of a plant by observing the system 
        performance under sustained instability and designers experimentally tune such algorithms.
        For example, from the input-output data of the selected actuators obtained in Fig.\ref{fig:openloop}, 
        it can be seen that a large integral action is needed to overcome the steady-state error.
        This is a common issue in low-cost DC motors, where the static friction of the gearbox presents 
        a nonlinearity which is most notable at low control authority and difficult to model. 
        
        Model-based control allows the designer to validate the performance of the system in simulation. 
        Often frequency domain tools are used to analyze the plant in an open loop. From this, a control law is designed around 
        the controllable state variables with physical information on the behavior of the system.
        Given a model of the system, designers also can formulate constraints, 
        and obtain an optimal control signal which meets these. For example, by minimizing the control effort in a cost function
        the challenges associated with choosing a saturation safety function can be mitigated.
        
        Parameter uncertainty is a common issue in controlling mobile robotics, and approximations of these often lead to 
        discrepancies between the mathematical optimal solutions found in simulation \cite{eide2011lqg} 
        and in real world performance \cite{tran2023fuzzy}. The difficulty with purely model-based approaches is
        the need for a high-fidelity model and access to low-uncertainty measurements of the state variables.
        
        A model of a TWSB robot, incorporating the non-idealities of low-cost DC motors is proposed by \cite{yamamoto2008nxtway}.
        It is used together with a simulation study of a WIP platform as a reference solution for the TWSB problem.
    
        Another approach is to use actuators with more favorable characteristics for the task at hand, such as stepper motors.
        The static balancing problem aims to control $\theta$ and regulate the linear displacement. The coupling of the 
        pitch angle to the rate of change in linear position requires active control, resulting in oscillations in both these state variables. 
        Stepper motors draw a nominal current, thus maintaining high torque at low speeds, eliminating the need for gearboxes and the 
        backlash associated with them. 
                
        The field of adaptive control proposes dealing with system uncertainties by designing controllers that may 
        learn over time. Online trial-and-error data and statistical techniques like regression-based transfer
        function estimation from input-output data are used to develop physics-informed models taken under statistical 
        distributions of belief \cite{benosman2018model}.         
                    
        In a similar vein, \cite{williams2016aggressive} embeds a neural network as an online function approximator to learn 
        predictions of the dynamics of the system. This prediction is then used as part of a trajectory planner in race-line optimization. 
        Some modern microcontrollers have sufficient computational power requirements needed for Model Predictive Control (MPC) and 
        effective implementations of convex optimizers \cite{nguyen2024tinympc} have been used in small mobile robots \cite{giernacki2017crazyflie}.
                
        An attractive aspect of predictive approaches to control is that they lend themselves naturally to 
        planning long horizons. These methods use numerical simulation techniques to evolve the system over time 
        and estimate the distribution of state probabilities through sampling of control actions. 
        The optimal control sequence is then chosen from these samples using a cost function.
                    
        The autonomous behavior of the TWSB robot explored in this paper is that of the path 
        following in an unknown environment, where no prior map is available. As such the 
        the control system has three goals, namely disturbance rejection of the pitch angle; 
        this is required such that the system is robust to the environment, minimizing 
        the linear displacement when stationary and tracking a trajectory obtained by a 
        high-level planner discussed in section 6. 
    
        A simple PID controller operating on the pitch error is tested in a simscape multibody; 
        a physics-based simulation where the control law is an applied force to a prismatic joint. 
        This force is coupled through the revolute joint to the pitch angle as described by \ref{eq:2DOF}.
        This manages to stabilize the pitch angle yet the $x$ position drifts over time as this 
        state variable is not controlled.
        More complete control laws are discussed in the following sections.
        \subsubsection{Controler requirements}

        The TWSB achieves balance by controlling the oscillations of the pitch angle about the 
        vertical axis. The linear system of equations in eq.(\ref{eq:2DOF}) is applicable 
        only when the pitch angle is small, this is taken to be $\theta < ±10$ degrees. 

        The advanced non-linear control methods discussed above are beyond the scope of this project. 
        Whilst their performance guarantees under real-world conditions are attractive, it is often simpler 
        to implement complex behaviors in the high-level planner.
        In the sequence, the low-level controls are developed to meet these requirements:
        \begin{enumerate}
            \item The pitch angle must be regulated to $±1$ degree.
            \item The robot must be able to safely recover from disturbances due to external forces and the environment.
            \item The robot must be able to track a reference velocity, with minimum overshoot.
        \end{enumerate}

        \subsection{Cascade PID}
                
        In the planer case shown in Fig.\ref{fig:WIP} the trajectory of the center of mass is parametrized by 
        the pitch angle $\theta$ and the linear velocity $v_b$. 
            
        A cascaded PID controller is used to control the pitch angle and the linear velocity. 
        Control of the position $(x_g,y_g)$ is left to a higher-level planner.  
        If the inner loop dynamics are much faster than the outer loop, 
        then the inner loop can be approximated as a disturbance \cite{Robust2DofPID}.

        Again, simscape multibody is used to verify the feasibility of this kind of controller Fig.\ref{fig:SimPID}.

        \begin{figure}[H]
            \centering
            
            \caption{Simscape Multibody Simulation of PID Cascade Controller regulating the linear velocity of the TWSB}
            \label{fig:SimPID}
        \end{figure}

        Through the Ziegler-Nichols method, the PID gains for each DC Motors speed control loop 
        are obtained. This process however may cause damage to the motors 
        during the sustained oscillations at the critical gain. 
        To determine the maximum operating frequency of the outer loop, 
        the inner motor speed loop is closed at 500Hz. Then the system is observed under chirp inputs to the motor, and from 
        these responses, the error of the pitch angle is subsequently regulated by a PID controller operating at 100Hz.
       
        This results in a stable system in 1DOF space. To minimize chatter in the pitch angle control signal, the outermost 
        loop controlling the body velocity is closed at 20Hz.
        The final cascaded closed loop PID controller is shown in Fig.\ref{fig:Cascade} with the gains in Table \ref{tab:PIDGains}. 
        This control system is able to adjust its target balancing point in such a manner as to come to an equilibrium, overcoming small 
        errors in the construction of the robot which might result in a center of mass that is not directly above the wheel axel. 
        Without the outermost loop controller, the TWSB is sensitive to this error and the offset must be tuned experimentally.

        \begin{figure}[H]
            
            \caption{Cascaded PID Controller}
            \label{fig:Cascade}
        \end{figure}

        \begin{table}[H]
            \centering
            \begin{tabular}{|r|r|r|r|c|c|c|c}
                \hline
                & \multicolumn{5}{c|}{Process Variable}  \\
                \hline
                Parameter & $v_b$ & $\theta$  & $\omega_L$ & $\omega_R$ & $\dot{\psi_b}$ \\
                \hline      
                $K_p$ & 3.5 & 0.19 & 2.4 & 2.9 & 0.7 \\
                $K_i$ & 0.8 & 5.6 & 24.8 & 24.8 & 0 \\
                $K_d$ & 0 & 0.003 & 0 & 0  &  0 \\
                \hline
            \end{tabular}
            \caption{Control system PID Gains}
            \label{tab:PIDGains}
        \end{table}
      
        \pagebreak{}
        \section{Navigation System}

        The TWSB robot is tasked with navigating around a track, marked by a line assumed to be of significant contrast to to its 
        surrounding environment. The performance of the navigation system can be characterized by the cross-track error and the lap time, 
        with the former being a critical failure mode, if the position diverges significantly from the track in a non-recoverable manner.

        \begin{figure}[H]
            \centering
            
            \caption{Test Track, (1) Chicane, (2) Hairpin, (3) Wall Proximity, (4) Straight, (5) Shallow Curvature, (6) Apex}
            \label{fig:TestTrack}
        \end{figure}

        The reference track tests common navigation tasks and challenges highlighted in Fig.\ref{fig:TestTrack}. 
        Here the environment is nonideal as the floor has various textures, marks, and colors.
        Lighting conditions are also nonuniform and the track is physically bounded by walls on all sides, enforcing hard accuracy constraints. 
        When teleoperated using the camera feed, it is challenging to avoid crashes. A human operator with 
        a full view of the environment can navigate the robot around the track, at moderate speeds the line is often lost 
        from the camera view. This mandates a corrective action using information about the robot's global pose, 
        which is not available to the TWSB. This track is therefore a suitability-challenging test for autonomous mobile navigation.
                   
        Map building is a popular approach for mobile navigation in a closed loop as it allows for a large 
        context of the environment to be considered. Closed maps can be built iteratively, by exploration 
        and subsequent loop closure. In this case, guarantees can also be made, 
        such as static obstacle avoidance and path selection by optimization functions \cite{Macenski_2020}. 
        This is referred to as global navigation and often requires advanced localization sensors 
        and algorithms to triangulate the robot's pose within the global environment.
               
        In this report, however, no global map data is available and the robot must navigate 
        the track using only the information obtained from the camera sensor. This is commonly known as local navigation
        and is fundamental to autonomous behavior where it is often impractical to obtain and maintain such a map. Without a map, 
        however, the robot must infer its pose relative to the track, and in cases where the track is not visible, the robot is lost. 
        Robust autonomy must be able to handle cases where the robot is lost, and safely search for the track or remain stationary. 
       
        Path following is commonly implemented with a lateral and a longitudinal controller. This follows from the 
        inputs and non holonomic constraints of the DDMR system in eq(\ref{eq:DDMRGlobal}).
        The longitudinal controller regulates the linear velocity of the robot where, in the simplest form, the reference speed 
        is set to a constant value, and the lateral controller keeps the robot heading aligned with the track. 
        This method is suitable for simple tracks and low speeds.
               
        In contrast, trajectory tracking is a method that generates some optimum path from the sensed environment and subsequently follows this path.
        This two stage process is falls under planning and is useful in cases where the lap time is more important than the cross-track error.
        In racing, the robot has to perform at the limits of its handling capabilities \cite{wischnewski2022indy}. Hence a method 
        for automatic safety is required, a common method extends planning by predicting the robot's position over some horizon,
        a velocity profile can be then obtained whilst maintaining the robot within certain bounds, often the profile is 
        designed in such a manner to stop the robot at the end of its horizon \cite{williams2016aggressive}. These kinds of model predictive controllers 
        have been demonstrated to have impressive performance but are complex methods that require a high-fidelity model of the robot within its environment. 
        The time constraints of this project preclude the exploration of data-driven 
        or learning methods employed to build such a model of the TWSB robot. As such a series of reactive controllers are used within different 
        racing-line algorithms based on curvature of the track ahead as baseline methods.
                   
        Many local navigation methods rely on obtaining a geometric representation of the track ahead, effectively building a local map.
        Commonly a path can be represented as a piece-wise arc or a form of cubic spline, from which parameters such as curvature, $\kappa$, 
        can be obtained. Simpler methods of path following by monocular camera have been applied to the TWSB robot, these do not measure the 
        geometry of the track, but rather use the image data to classify a set of features and use these in a rule-based algorithm to follow the 
        track, \cite{visionlinetwsb} \cite{ismail2009vision} \cite{nntwsbvision}.
        These methods are found to limit the track to shallow curvature or low speeds as they only utilize a small 
        a subset of the information available from the camera sensor. 
       
        In this paper, a method is developed that obtains a set of track waypoints from a grayscale monocular camera. 
        Whilst these do not predict the future poses of the robot, the nature of the 
        monocular camera sensor's information allows for a dynamic velocity component to be added to path following.

        \subsection{Camera Sensor}
        Geometric information about the track can be observed from a camera sensor mounted on the TWSB robot.
        This obtains a discreet 2D projection of the environment in the form of a matrix of pixels, each of which encodes 
        its value as an 8-bit unsigned integer. Considering such an image, it is nontrivial to
        obtain a map of the track concerning the robot, as the data is highly encoded in a large measurement space. 
        Perceptual sensors of this form differ from the physical sensors found elsewhere on the TWSB robot as the quantity measured; 
        light intensity, is not directly usable as a state variable, except in simple autonomous behavior like photo-taxis \cite{hasslacher1995living}. 

        The question of what quantifies useful information in an image is a long-standing problem,  \cite{siegwart2011introduction} classifies 
        perception as the process of condensing the detailed information contained within each image, or sequence of images, 
        into features that are useful to track for the task at hand.
        In the case of monocular mobile navigation, the notion of feature models is a key concept in active perception \cite{Activeperception}.
        These models are used to infer $\textit{percepts}$, which are then used to make decisions in controlling the robot's pose within its environment 
                \cite{hutchinson1996tutorial}. 

        The field of computer vision is concerned with the extraction of these percepts from the image data. 
        Classical computer vision algorithms are used to extract spatial information about the sensed environment over the visible 
        horizon. Common features are reasoned by geometry, \cite{lee2009geometric} such as edges, corners, lines, and blobs of texture. 
        These are typically processed using a series of 2D convolutional filters, or kernels, which for large images is
        computationally expensive and often requires the use of a GPU to parallelize the operations. In these cases, the
        advances in parallel computing have proliferated the use of neural networks in computer vision, which apply a 
        series of latent filters to the image data. These are trained on large datasets of images 
        or online \cite{tai2017virtual} \cite{lee2013line} \cite{kober2013reinforcement}, and aim to simply the process of feature extraction. 
                
        The TWSB is equipped with a Raspberry Pi Camera Module V3, which is a rolling shutter camera. Images are obtained 
        in grayscale directly from the Y plane of the camera driver at 640x480 resolution to improve encoding speed and 
        minimize wireless transmission bandwidth.

        \subsubsection{Calibration}
        Cameras are optical devices and are subject to lens and pixel distortion. Modern cameras are assumed to have square pixels, 
        but still require some calibration to undistort the barrel effect of the lens. 
        The camera is mounted on the TWSB robot at a height of 18cm with an angle of 15 degrees to the floor plane.
        This perspective results in rectangles in the environment being projected into trapezoids.  This makes it difficult to 
        obtain distances between different features identified in the image \cite{tuohy2010distance}
        A top-down, orthographic view of the floor plane is desired, where there is a linear function mapping pixel sizes 
        to real-world distances. A chessboard pattern of known dimensions is placed on the floor plane in front of the camera, 
        this encompasses the entire field of view. From the position of the chessboard corners in the image, 
        a homography matrix is obtained which maps the image coordinates to the real-world coordinates \cite{bradski2008learning},
        resulting in the corrected perspective transform shown in Fig.\ref{fig:perspective}. 
        This method assumes the pitch angle, and thus its field of view of the camera to be constant, it it diverges too much the 
        mapping needs to be re-calibrated which is computationally expensive on the Raspberry Pi.
        \begin{figure}[H]
            \centering
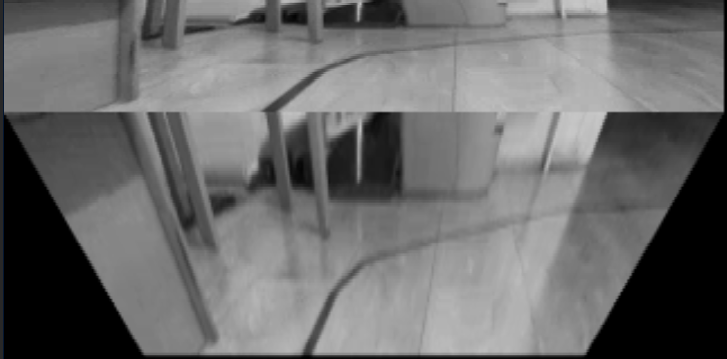
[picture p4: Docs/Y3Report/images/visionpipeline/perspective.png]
            
            \caption{Perspective Correction}
            \label{fig:perspective}
        \end{figure}

        \pagebreak{}
        \subsection{Track Detection}
        The robot must be able to obtain an estimate of where the track line is, relative to its forward direction.
        In nonideal environments, significant noise is present in the image data, 
        and simple edge thresholding methods are not sufficient. This noise can lead to large errors
        in the estimated position of the track. The information in the image needs to be condensed into a set of features
        that describe the track. Summing the pixel values in each column, a distribution of the edges 
        across the image is found. The ideal straight line can be thought of as a single peak in the center of the frame.  
        It can be seen in Fig.\ref{fig:Line Detection and Segmentation} that this method results in peaks of different 
        shapes depending on the curvature of the track, however, the track position in the image plane is readily 
        segmented by the peak's topological prominence, that is the difference between 
        a peak and the local minima around it. 
        \begin{figure}[H]
            \centering
            \begin{subfigure}[b]{0.45\textwidth}
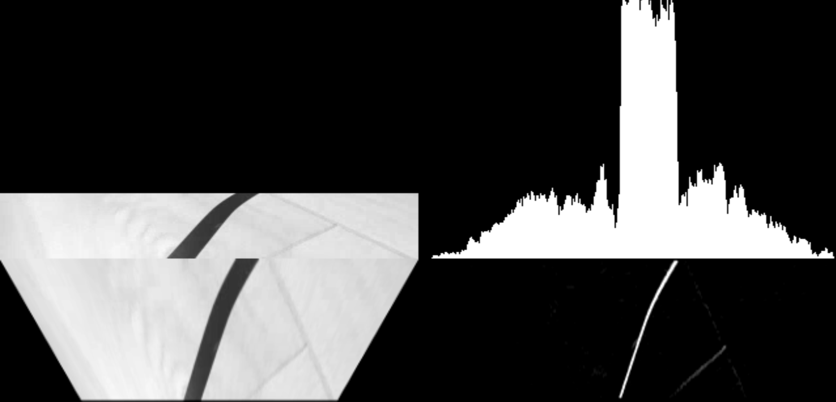
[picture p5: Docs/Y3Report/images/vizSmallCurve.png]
                
                \caption{Low Curvature}
                \label{fig:LineDetection}
            \end{subfigure}
            \hfill
            \begin{subfigure}[b]{0.45\textwidth}
                
                \caption{Sharp Curvature}
                \label{fig:Sharp Curvature}
            \end{subfigure}
            \caption{Line Detection and Segmentation}   
            \label{fig:Line Detection and Segmentation}
        \end{figure}
        
        Some challenging cases, where simpler methods may fail, are shown in 
        Fig.\ref{fig:ChallengingEnvironments}. Here it can be seen that these cases have a higher noise floor, 
        that is the the peak is not as prominent. This prominence can be used as an indicator of the confidence that 
        the peak is the true position of the track. 

        \begin{figure}[H]
            \centering
            \begin{subfigure}[b]{0.45\textwidth}
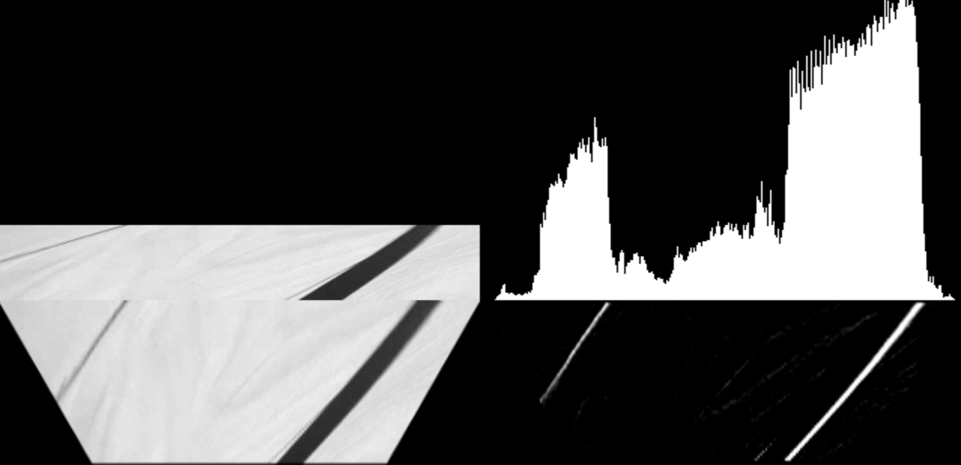
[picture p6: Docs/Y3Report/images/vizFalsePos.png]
                
                \caption{False Positives}
                \label{fig:FalsePositives}
            \end{subfigure}
            \hfill
            \begin{subfigure}[b]{0.45\textwidth}
                
                \caption{Reflective Occlusion}
                \label{fig:ReflectOcclusion}
            \end{subfigure}
            \caption{Challenging Environments}
            \label{fig:ChallengingEnvironments}
        \end{figure}

        False positives as shown in Fig.\ref{fig:FalsePositives} are a serious issue with line detection algorithms as 
        they often cause the robot to lose track of the original path in a nonrecoverable manner.
        These are difficult to remove once present in the 1D histogram of the edges, as they form peaks of similar shapes to desired features. 
        This nonunique mapping of data to a set of features is a common issue in robotic perception, as such the control and perception methods 
        must be co-designed to reject these robustly.

        From these images, three sources of noise features are identified: salt and pepper noise, arising mainly through impulses in texture 
        variation of the floor, object boundaries resulting in an edge of a similar shape to the track, and occlusions from reflections 
        or movement blur stemming from the rolling shutter of the camera.

        Pre-filters like the median filter can be used to remove salt and pepper noise, however, this is computationally expensive, taking on average 10ms
        to process a single frame on the selected hardware; resulting in the entire pipelining not running in real-time. 
        The proposed vision pipeline uses morphological operators to modify the shape of the features in the image.
        By eroding and dilating these features, the impulse noise is removed, this lowers the median noise floor, increasing the prominence of the peaks. 
        Assuming that the robot is initially on the track, then the search space for the peak representing the track can be expanded around the last
        known position of the track. Subsequently, the track peak is searched for staring at the bottom of the image, and sliding a window upwards, 
        until a large discontinuity is found. This is done by searching for the largest peak in the histogram, warm starting each section search from the position 
        of the peak found in the section below it, and then checking if the next peak is within a certain distance. In this manner,
        a series of waypoints on the track is obtained, which as shown in Fig.\ref{fig:LineDetection} are robust to the sources of noise discussed. 
        The algorithm processes each frame and obtains a continuous set of waypoints describing the track on average in 0.15ms when running on the Raspberry Pi 5.
        \begin{figure}[H]
              \centering
              \begin{subfigure}[b]{0.32\textwidth}
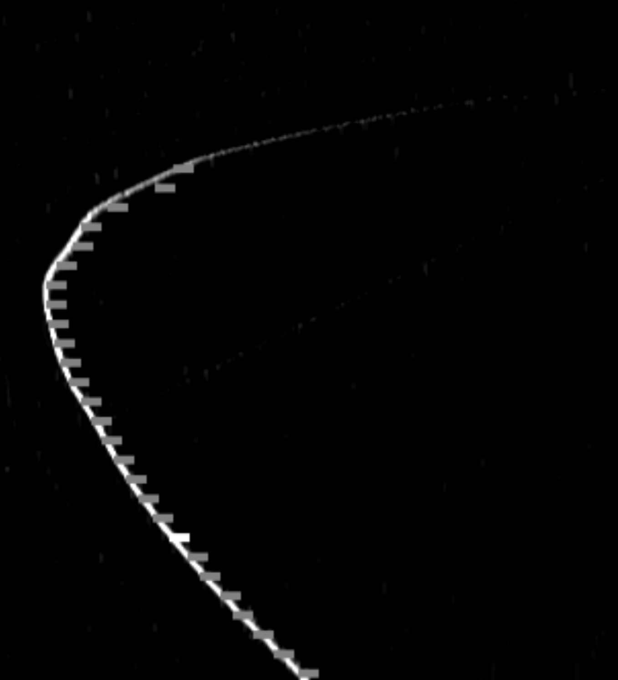
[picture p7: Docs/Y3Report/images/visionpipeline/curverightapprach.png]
                 
                 \caption{Right Curve Approach}
                 \label{fig:appoachRight}
              \end{subfigure}
              \hfill 
              \begin{subfigure}[b]{0.32\textwidth}
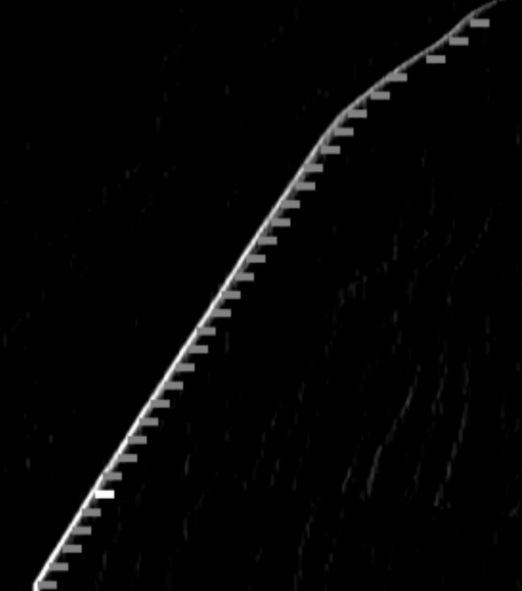
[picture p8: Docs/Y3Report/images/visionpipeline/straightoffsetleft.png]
                 
                 \caption{Off Straight}
                 \label{fig:straight} 
              \end{subfigure}
              \hfill
              \begin{subfigure}[b]{0.32\textwidth}
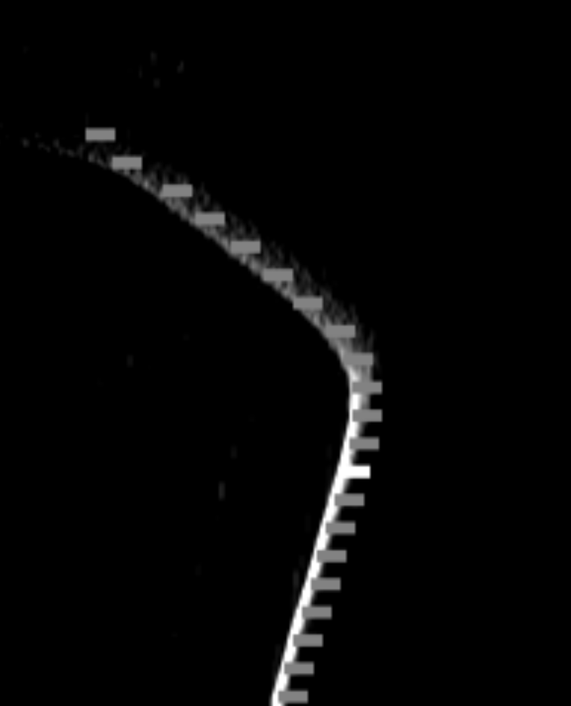
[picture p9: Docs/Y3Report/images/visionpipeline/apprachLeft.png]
                 
                 \caption{Exit Chicane}
                 \label{fig:exitChicane}
              \end{subfigure}
              \caption{Path Waypoints}
              \label{fig:PathWayPoints}
           \end{figure}

        \begin{figure}[H]
            \centering
            
            \caption{Local Waypoint Following}
            \label{fig:PurePersuit}
        \end{figure}

        \pagebreak{}
        \subsection{Racing Algorithms}
            \subsubsection{Lateral Control}

            A bang-bang-type steering controller is used to obtain a baseline track performance. 
            This is a reactive controller which uses the cross track error, obtained via a topological peak tracker as described in section 6.2.
            In this case, the velocity target of the robot is set to some constant value. 
            The virtual sensor is applied to a small section of the bottom of the image frame, representing points on the track that are closest to the robot. 
            This manages to navigate the track without losing it on straights and gentle curves, however, it suffers on
            sharp sequences of curves, and chicanes, where the track in the observed section is lost or degraded. In this case, by rolling off the last known position 
            of the track towards the center of the image at each frame sample, and setting the velocity target to zero when no line is detected,
            the robot can navigate the track past the chicane. This control method is not robust or reliable and few trials can be performed where 
            the robot does not lose track and is forced to come to a stop.
            Despite the limitations in path-following accuracy, this simple method is capable of completing laps of the track at a
            low speed, \( v_{\text{max}} \ll 0.3 \, \text{m/s} \).
            This can be attributed to the implicit look ahead in the vision system, shown in Fig.\ref{fig:PurePersuit}, where the bottom of the image frame 
            captures the track some distance ahead of the robot and not exactly at its current position.

            \subsubsection{Adaptive Lookahead and Longitunal control}
            Constant parameter tuning is undesirable in a racing context as the robot must be able to adapt to the environment.
            Lookahead distance is one of such parameters that are often fixed or tuned experimentally,
            towards better racing performance, the failure cases of understeering on curves and oversteering on straights 
            are improved in 2 manners. The linear velocity of the robot is set to be inversely proportional to the number of waypoints found vision system,
            as this represents how much track there is ahead of the robot. This implicitly slows the robot down as it approaches a curve, 
            and handles adverse environmental conditions such as occlusions in the track automatically predictably, and safely. 
            It allows it to accelerate on a straights. By entering the cures at a lower speed, the robot no longer loses the track from its frame. 

            The chicane now poses a different challenge, as the robot must enter it slowly but it is desirable to accelerate out of it.
            Considering that upon entering the chicane, the longitudinal controller slows the robot down, so more of the track is visible, 
            hence to accelerate out of the curve the lookahead distance is increased inversely proportional to the number of waypoints. 
            This approach is counterintuitive as commonly, on straights, the looked distance is increased 
            and decreased on curves, however in the case of the TWSB robot, when the lookahead distance is too small the dead zone
            in the vision system causes the track to leave the image frame on sharp curves such at the apex of
            the chicane. By increasing the lookahead distance robot takes shallower turns, notably on the hairpin section of the track, enabling it to 
            increase its speed as the robot obtains a waypoint that is past the apex of the chicane allowing it to accelerate out 
            of the curve. This late apex racing strategy is commonly used by human racing divers \cite{kegelman2017insights}.
        
    \pagebreak{}

  %%%%%%%%%%%%%%%%%% SECTION 4 %%%%%%%%%%%%%%%%%%
  \section{Results and discussion} % edit section heading as appropriate
    \subsection{Balance Performance}

    A set of experiments are performed on the TWSB to evaluate the suitability of the controller designed in section 5 for the task of racing. 
    Data is collected at 100Hz and timestamped to ns resolution using the Raspberry Pi's internal clock. 

    The TWSB is righted from rest to a vertical position on a flat surface and the controller is activated. 

    \begin{figure}[H]
        \centering
        
        \caption{Balance Performance}
        \label{fig:BalancePerformance}
    \end{figure}

    Fig.\ref{BalancePerformance} shows the 
    distribution pitch angle and x position as measured by the robot's sensors. 
    This experiment addresses the static balancing problem of the TWSB system, it was run continuously for 95 seconds,
    after which it was manually stopped. The results demonstrate that the robot maintains its position within ±1 mm 
    while regulating its pitch angle within ±1° of the vertical. The pitch distribution exhibits a sharp mode centered
    at approximately $-0.3\deg$, indicating a consistent, small offset from the theoretical upright equilibrium. 
    In contrast, the X position distribution is broader, with a relatively uniform frequency across the range. 
    This reflects low-amplitude, periodic oscillations in wheel position, which are intrinsic to the balancing process. 
    These oscillations result from the control effort required to counteract destabilizing torques and maintain upright stability. 
    Given that the 1 mm deviation represents less than $0.5\%$ of the wheel circumference.
    it can be concluded that the robot effectively maintains a static balance with negligible positional drift.
    \begin{figure}[H]
        \centering
        
        \caption{Disturbance Rejection}
        \label{fig:DisturbanceRejection}
    \end{figure}

    In the experiment shown in Fig.\ref{fig:DisturbanceRejection}, the robot is subjected to a series of external disturbances. 
    Rough terrain, including small household objects such as pens, coins, and other irregular items, is placed in its path. 
    Additionally, large impulsive forces are applied manually at approximately sample times $k = 800$ and $k = 3200$. 
    These disturbances displace the robot from its equilibrium, prompting it to regain balance by accelerating forward.
    Interestingly, even though the $x$ position is not explicitly regulated by the control system, 
    the TWSB robot gradually returns to its original position. As the robot traverses the small obstacles during this recovery, 
    minor oscillations are observed in the $x$ position signal, superimposed on the decaying trend back to zero.
    The pitch angle also responds to the disturbances, exhibiting transient overshoot relative to the 
    target angle  $\theta_{\text{trgt}}$. These results confirm the robot's ability to reject both terrain-induced 
    and impulsive external disturbances, while maintaining dynamic stability.

    \subsection{Velocity Tracking}

    Before testing the robot in a race track environment it must be verified that it can track velocity setpoints, accelerate, and most 
    importantly decelerate whilst maintaining balance. 
    \begin{figure}[H]
        \centering
        
        \caption{Velocity Tracking}
        \label{fig:VelocityTracking}
    \end{figure}

    In the experiment shown in Fig.\ref{fig:VelocityTracking}, the robot is commanded via a series of 
    ramp step functions to accelerate and decelerate at a constant rate. These aim to replicate the kinds of reference velocity profiles 
    the robot will have to perform if it is to achieve good lap times.
    The TWSB exhibits some minor lag in response tho the reference velocity, there is also some overshoot, which is 
    more significant when large decelerations are commanded. This can be attributed to the non-minimum phase of the system, 
    where the robot must first accelerate before it can decelerate, supplementing the velocity control with an acceleration 
    profile is a possible solution to this problem. Again, it can be seen that throughout this experiment the linear displacement 
    is driven to its 0 position when no velocity is commanded, even under large internal forces, this is a positive indication that the robot is able
    to perform well at its handling limits. In this experiment velocities were commanded up to 2 m/s, as above this the motors enter saturation 
    if operated continuously.

    \subsection{Path Following}
    The TWSB robot is tested on the track shown in Fig.\ref{fig:TestTrack}. Fiducial Markers are placed at the start position of the track and on the robot itself. 
    These are used by a top-down camera fixed to the ceiling, to track the position of the robot across many laps. The camera captures video at 30Hz in 1920x1080 resolution.
    The OpenCV library is used to track the April Tag on the robot, however, due to motion blur at high speeds it is unsuccessful in tracking the robot at all times, and 
    suffers especially on the straight section of the track where the robot is at its maximum velocity. Nevertheless, the obtained points are included in this analysis 
    as they provide a good indication path path-tracking performances, especially on the corners and other slow sections of the track. It also serves to demonstrate the discrepancies 
    between the real world, global localization, and the significant drift in position in the robot's inertial odometry. 

    A total of 80 Laps of the track were performed and recorded recorded several trials, these all used the same parameters for the controller but different limits on maximum velocities. 
    At each trial, the robot was reset to the start position and completed numerous laps of the track in a row. There was no human intervention in the control of the robot,
    and the separate trials were implemented as necessary for data collection.  The position of the tracker as sampled by the top-down fiducial tracker within its camera frame is 
    shown in Fig.\ref{fig:TrajTrack}. The track is obtained by common image processing contour extraction techniques.

    \begin{figure}[H]
        \centering
        
        \caption{Top Down Fiducial Tracker}
        \label{fig:TrajTrack}
    \end{figure} 

    Here it can be seen that the robot is generally able to navigate the track. There are some cases where the position diverges from the rest 
    of the laps, notably about the first apex of the chicane, where occasionally there is some overshoot in position. The TWSB is still able to regain the track 
    and complete the lap in these cases. Further discussion of this is provided in section 7.4.
    As alluded to in the design of the waypoint tracking algorithm, adaptive changes to the lookahead distance, as denoted by the white marker in 
    Fig.\ref{fig:PathWayPoints}, causes the TWSB slightly understeers on entering the chicane and exiting the hairpin section of the track. 

    \subsection{Race Performance}

    The TWSB robot can consistently complete laps of the track. The figures below show the global position of the robot 
    as obtained by its odometry model, these are from the same trials as the fiducial tracking data. The discrepancy in the shape of the mapped track, and thus the 
    position accuracy of the robot is expected and is attributed to drift in odometry. Interestingly the odometry maps have a similar shape and begin diverging at sharp 
    curves, possibly due to the feathering of the linear and angular velocity increasing quantization errors at low speeds. Nevertheless, since the fiducial marker  
    is unable to obtain the global velocity profile of the laps, these figures provide an appropriate visualization for the discussion of the racing algorithm and strategy. 
    The robot travels clockwise around the track, and the start position is marked with a blue dot. The increase in maximum velocity of the TWSB between 
    Fig.\ref{fig:Slow Lap} and Fig.\ref{fig:Fast Lap} can be seen by the increase in track length where the robot exerts its maximum velocity, this is especially notable in the curves 
    where due to the faster velocity the robot can accelerate and decelerate in between corners, as opposed to a smooth constant velocity as seen in the slow lap. 
    At the chicane, the fast lap slows almost to a halt since it enters it a a speed greater than the maximum velocity achieved in the slow lap. Exiting the chicane it also accelerates smoothly 
    until it reaches the next corner. This is different from the baseline controller which does not implement the adaptive lookahead distance method and so takes the next corner gradually
    by threading the throttle as can be seen by the sections of low velocity in Fig.\ref{fig:baseline}. 

    In Fig.\ref{fig:Fail Recovery} the robot is shown to be able to recover from losing the track. Upon exiting the hairpin, it overshoots as 
    it did not slow down in the section that Fig.\ref{fig:Fast Lap} did. This causes a sudden stop, and the robot is required to turn slowly until it rejoins the track. 
    A similar case happens on exiting the chicane, where the robot has entered it at close to maximum velocity, and the track is lost. Again the TWSB comes to a sharp stop and manages to recover the 
    track. Even through these failures, the lap time is still significantly faster than the baseline and slow test lap. This indicates that if a good recovery system is in place 
    the robot can be pushed to its limits safely.

    Attempts were made to increase the maximum velocity of the robot to 2 m/s in line with the experiments in section 7.2, however with an acceptation profile, the pitch angle would 
    tilt too far back during sections of such high velocity causing the track to be completely lost from the camera frame, this in turn slowed the robot down but it was unable to recover the track 
    estimate and reliably complete more than 10 continues laps. Possibly a larger section of a straight would allow the robot to accelerate to this speed and then regulate the pitch
    angle to maintain the track, however this was not tested in this report.
   
    \begin{figure} [H]
        \centering
        \begin{subfigure}[b]{0.48\textwidth}
            
            \caption{Slow Lap}
            \label{fig:Slow Lap}
        \end{subfigure}
        \hfill
        \begin{subfigure}[b]{0.48\textwidth}
            
            \caption{Fast Lap}
            \label{fig:Fast Lap}
        \end{subfigure}
        \caption{Best Laps}
    \end{figure}  

    \begin{figure} [H]
        \centering
        \begin{subfigure}[b]{0.48\textwidth}
            
            \caption{Baseline Controller}
            \label{fig:baseline}
        \end{subfigure}
        \hfill
        \begin{subfigure}[b]{0.48\textwidth}
            
            \caption{Recovery From Loosing Track}
            \label{fig:Fail Recovery}
        \end{subfigure}
    \end{figure}

  %%%%%%%%%%%%%%%%%% SECTION 5 %%%%%%%%%%%%%%%%%%
  \section{Conclusions and future work} 
  \subsection{Conclusions}
    The experiments demonstrate that the hierarchical PID control strategy implemented for the two-wheel self-balancing robot is 
    highly effective in addressing both static and dynamic balance requirements, as well as the demands of a racing environment.
    During static balance tests, the robot maintained its pitch angle within $\pm1^\circ$ of the vertical and exhibited positional 
    deviations confined to within $\pm1$~mm, demonstrating negligible drift.
    Such precision confirms the efficacy of the control system in countering intrinsic oscillations and maintaining stability even under minor disturbances.

    In dynamic scenarios, the robot proved its robustness by effectively rejecting external disturbances.
    When subjected to irregular terrain and impulsive forces, the system transiently overshot in both pitch and position but quickly recovered 
    and returned to the desired equilibrium. This behavior underscores the controller's ability to counteract sudden perturbations
    while preserving overall stability. Additionally, the velocity tracking experiments revealed that the robot can accurately follow acceleration and 
    deceleration commands representative of race conditions, despite experiencing minor lags and overshoots. 
    These transients, attributed to the non-minimum phase nature of the system, did not detract from the robot's overall dynamic performance as it successfully returned 
    to its neutral state when no velocity was commanded.

    The path-following tests, which relied on a ceiling-mounted camera and fiducial markers, further validated the system's navigation capabilities over multiple 
    laps on a test track. Although high-speed motion induced occasional tracking inaccuracies due to motion blur, the adaptive waypoint tracking algorithm was effective
    in adjusting lookahead distances and ensuring that the robot maintained a predominantly correct path. This was particularly evident in curved sections, 
    where the robot's capacity to navigate corners through controlled acceleration and deceleration yielded improved lap times compared to a baseline controller.

    Ultimately, the successful integration of the hierarchical control strategy, along with the clear separation of subsystems, has resulted in a platform that is 
    both robust and adaptable. The experimental evidence suggests that taking a design approach which abstracts layers of autonomy allows for a system, which combined with its subsystems
    exceeds the performance requirements for a high-speed, agile two-wheel self-balancing robot. The system's ability to maintain balance, track desired velocities, 
    and recover from deviations highlights its potential for application in competitive environments, while also providing valuable learning and educational insights 
    for future enhancements in sensor fusion control and navigation strategies.
    \subsection{Future work}

    This project has successfully demonstrated the feasibility the a two-wheel self balancing robot designed in racing a a track at its limits of handling. 
    However, several areas for future work could enhance the performance and capabilities of the system. Firstly the system is currently reliant 
    on local odometry, and the top down camera fiducial tracker is inadequate for high-speed capture due to motion blur, as such a preliminary area of research 
    should be in obtaining, validating or designing a system which can accurately track the robot in an indoor environment in real-time to obtain accurate and reliable positional 
    data, this could be achieved using a combination of multiple cameras, Ultra Wideband position sensors or directly embedded a Lidar sensor on the robot. Once localization is achieved 
    the platform improvements to the local navigation can be made and verified such as obstacle avoidance, and global trajectory optimization can be made for achieving higher laps speeds. 
    Whilst an LQR might provide some design assurances, it is believed that larger performance gains could be achieved through developing a data driven or 
    learned model of the racing dynamics of the platform. Improvements can also be made to the mission algorithms, which currently only consumes $10\%$ of the Raspberry Pi's CPU time, 
    and so more data can be processed such as implementing optical flow for dynamical projecting the bird's eye view of the track.

  %%%%%%%%%%%%%%%%%% REFERENCES %%%%%%%%%%%%%%%%%%
    \printbibliography
  %%%%%%%%%%%%%%%%%% APPENDICES %%%%%%%%%%%%%%%%%%
  \begin{uomappendix} 
      \section{Code}
      The repository for this project can be found at 
      https://github.com/Wrodders/dBot
      \section{Risk assessment}
    
    \section{Project plan}
    
    \section{Continued Professional Development}
    
      
  \end{uomappendix}

  %%%%%%%%%%%%%%%%%% END MATTER %%%%%%%%%%%%%%%%%%
  \end{document}

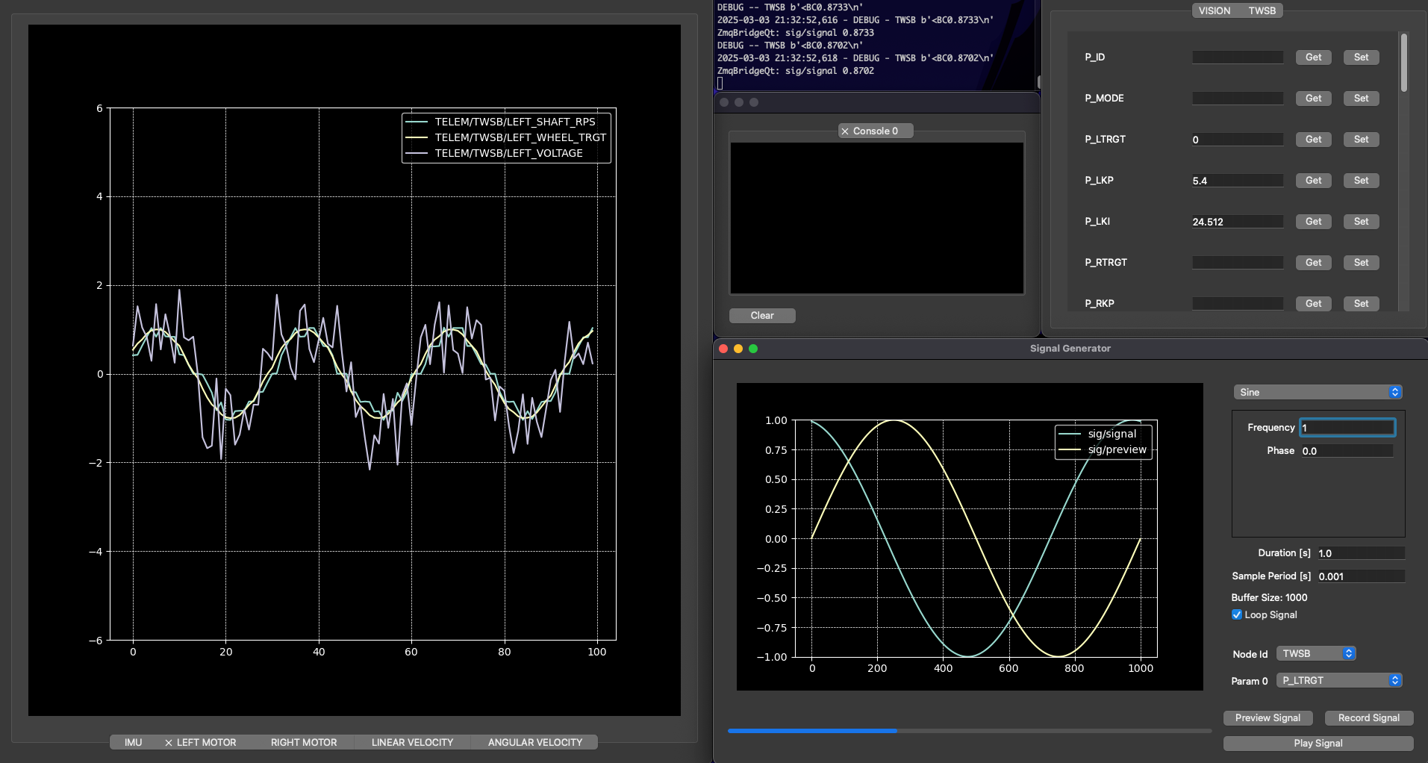
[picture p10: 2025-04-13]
Docs/Y3Report/images/visionpipeline/SysIDMotorSetUp.png

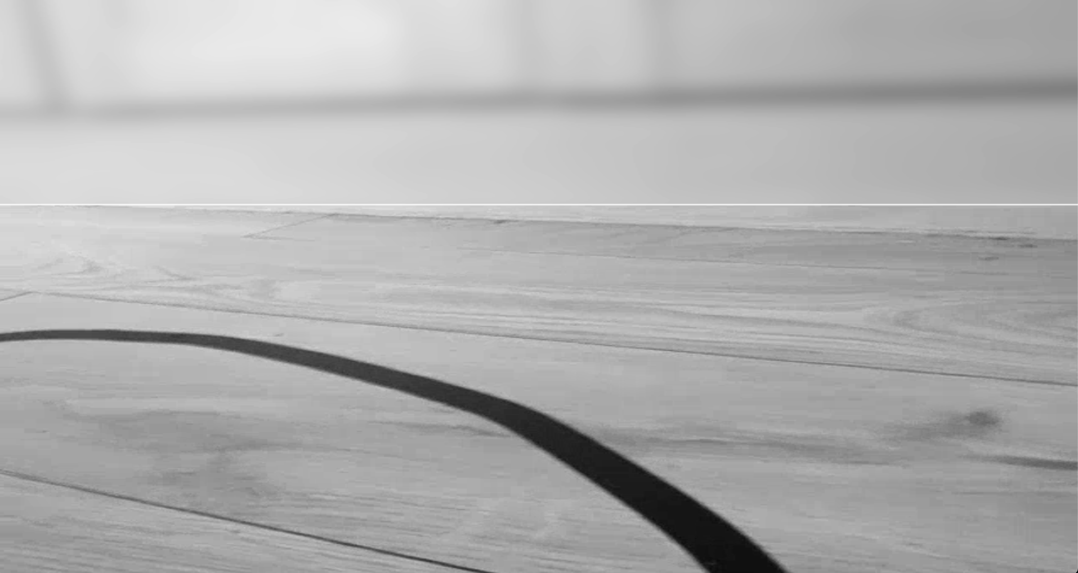
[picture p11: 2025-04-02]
Docs/Y3Report/images/visionpipeline/WallCuveLeft.png

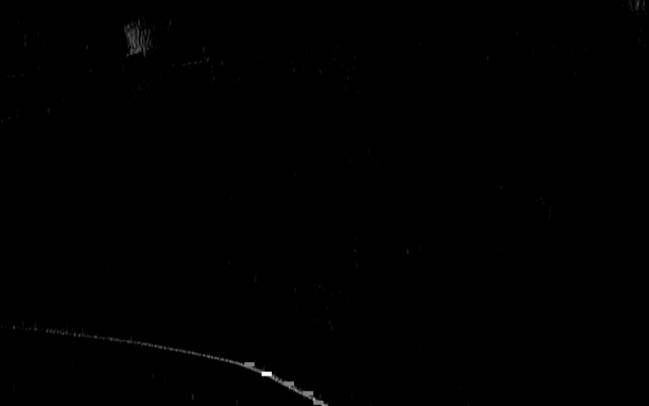
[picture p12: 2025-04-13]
Docs/Y3Report/images/visionpipeline/sharpcurveleft.png

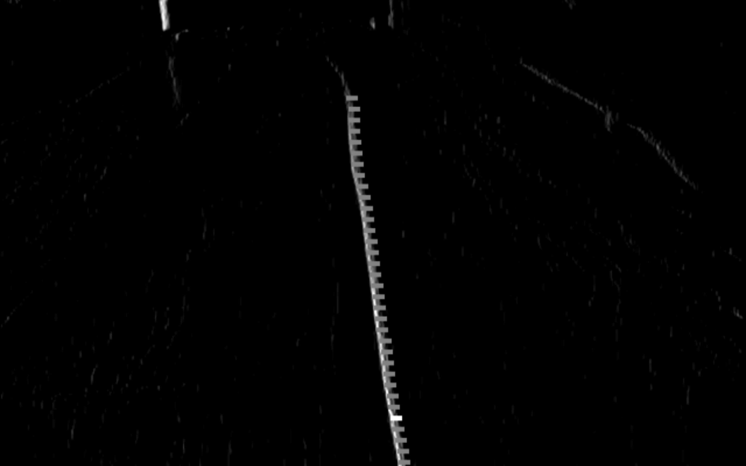
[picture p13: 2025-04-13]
Docs/Y3Report/images/visionpipeline/straight2.png

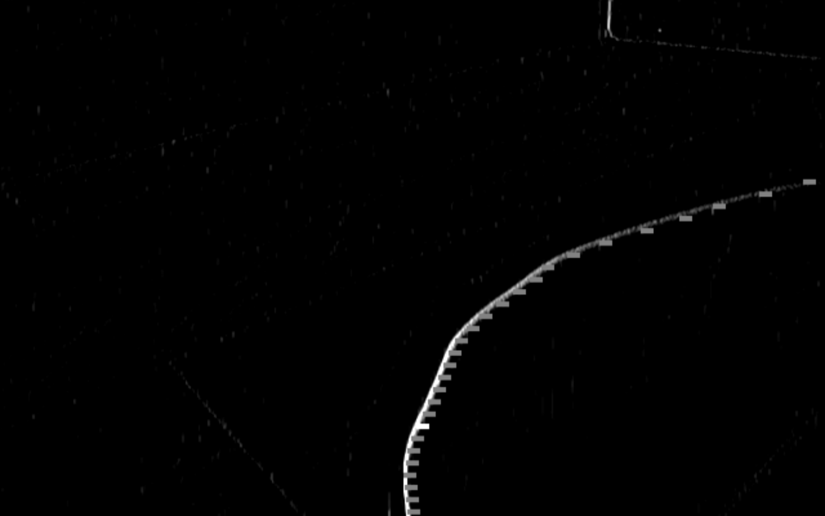
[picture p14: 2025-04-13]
Docs/Y3Report/images/visionpipeline/curverightenter.png

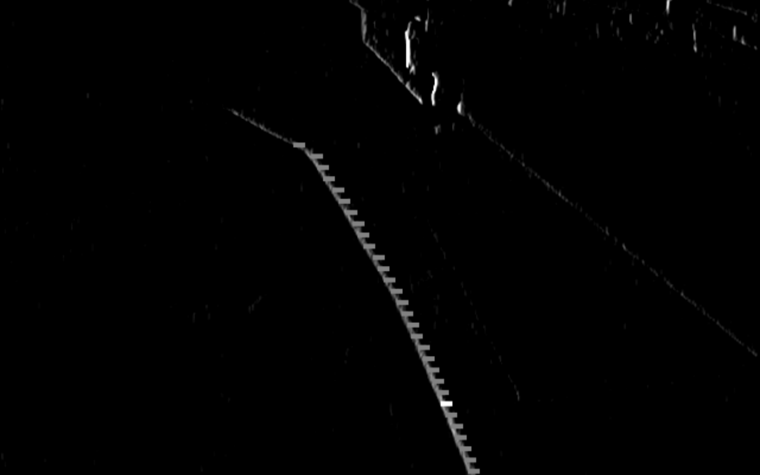
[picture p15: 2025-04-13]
Docs/Y3Report/images/visionpipeline/envnoisestraight.png

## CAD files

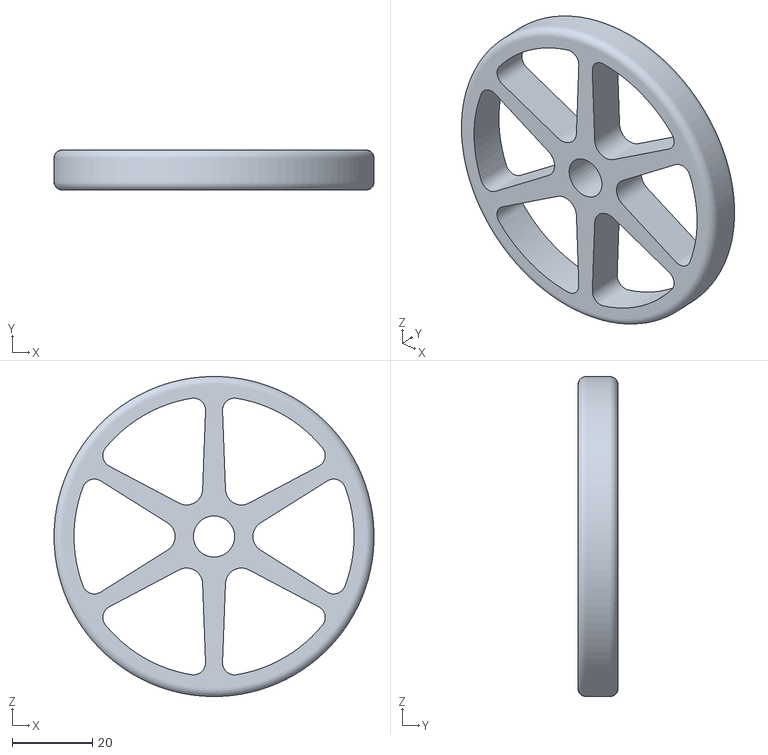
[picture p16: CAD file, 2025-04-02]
Hardware/CAD/Wheel.stl
80.0 x 10.0 x 80.0

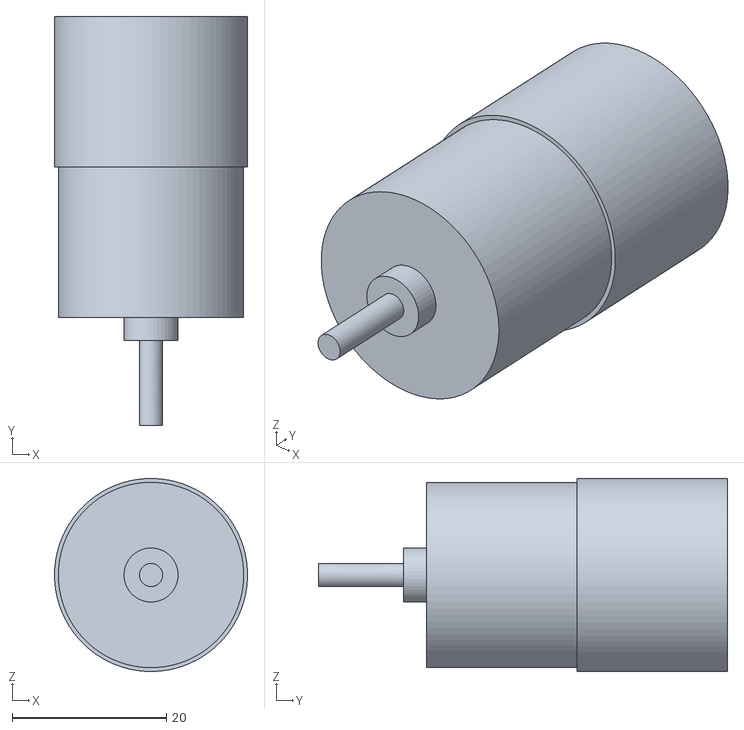
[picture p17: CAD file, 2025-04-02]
Hardware/CAD/DCMotor.stl
25.0 x 53.0 x 25.0

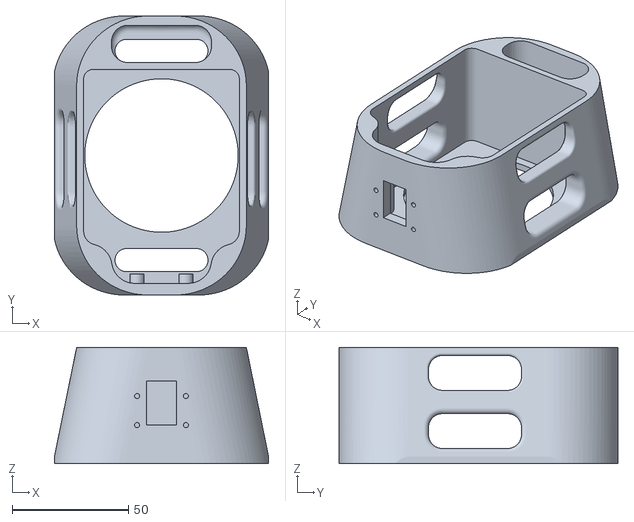
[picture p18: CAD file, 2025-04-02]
Matlab/CAD/Head.stl
92.1 x 120.0 x 50.0

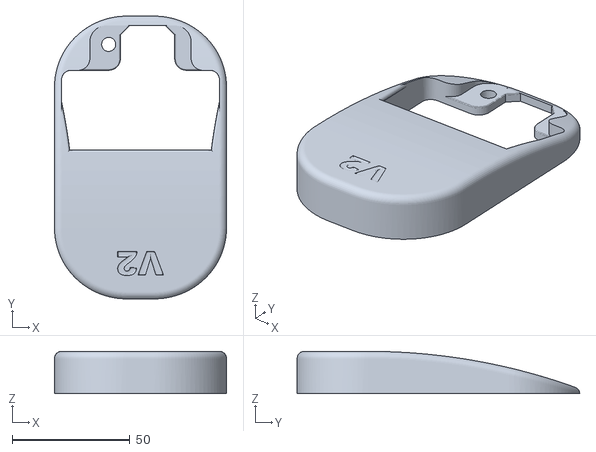
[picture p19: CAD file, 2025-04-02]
Hardware/CAD/Top.stl
73.0 x 120.0 x 18.0

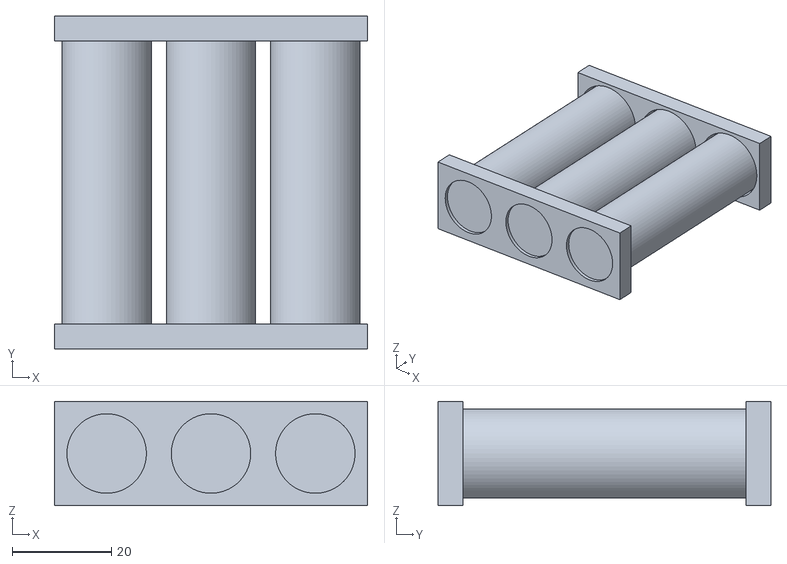
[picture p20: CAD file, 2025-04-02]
Matlab/CAD/BatteryPack v23.stl
63.0 x 67.0 x 21.0

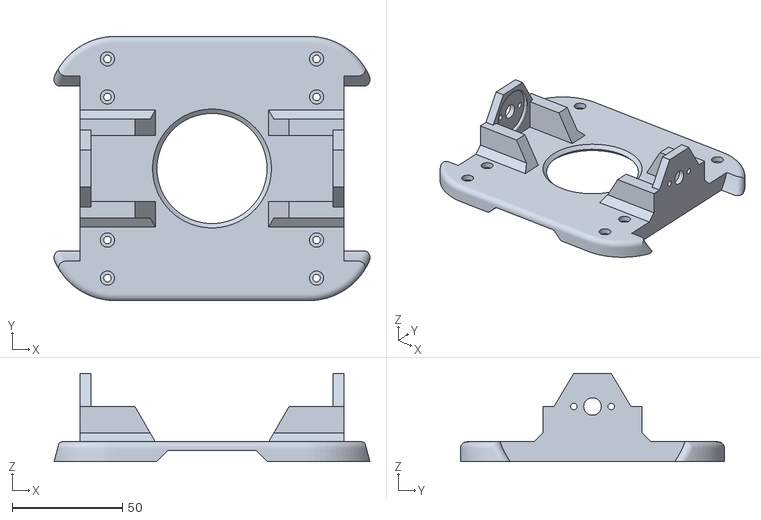
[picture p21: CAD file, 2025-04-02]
Hardware/CAD/Chassis.stl
143.5 x 120.0 x 40.0

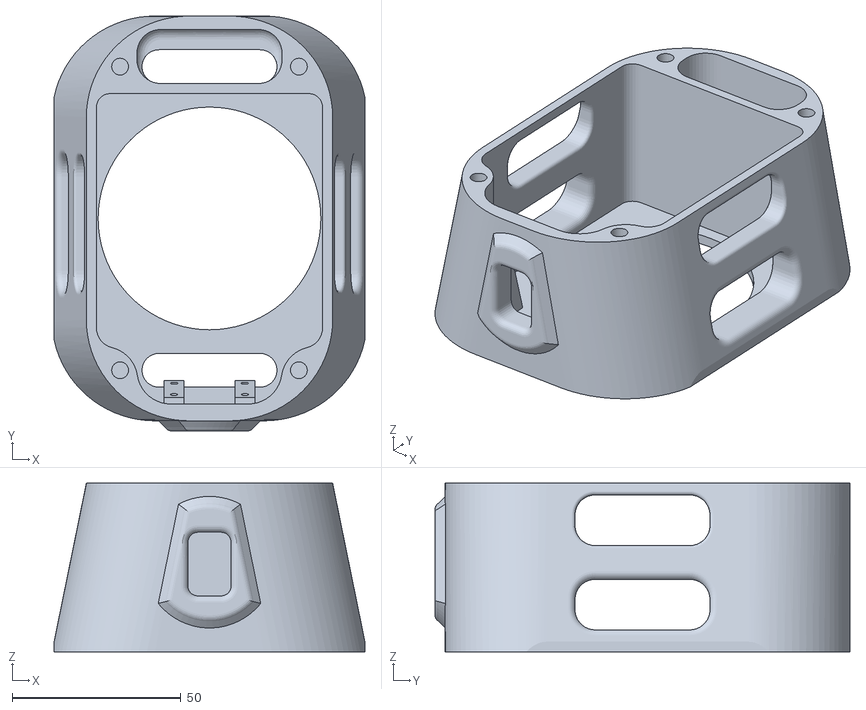
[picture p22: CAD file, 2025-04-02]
Hardware/CAD/Head.stl
92.1 x 123.0 x 50.0

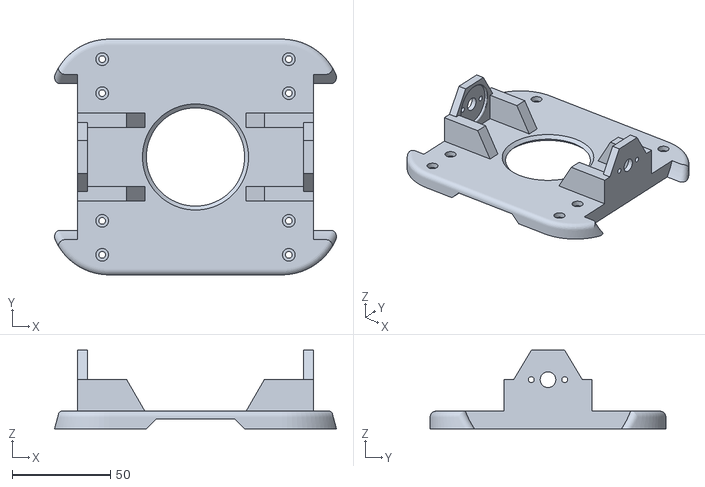
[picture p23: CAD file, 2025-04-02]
Matlab/CAD/Chassis.stl
143.5 x 120.0 x 40.0

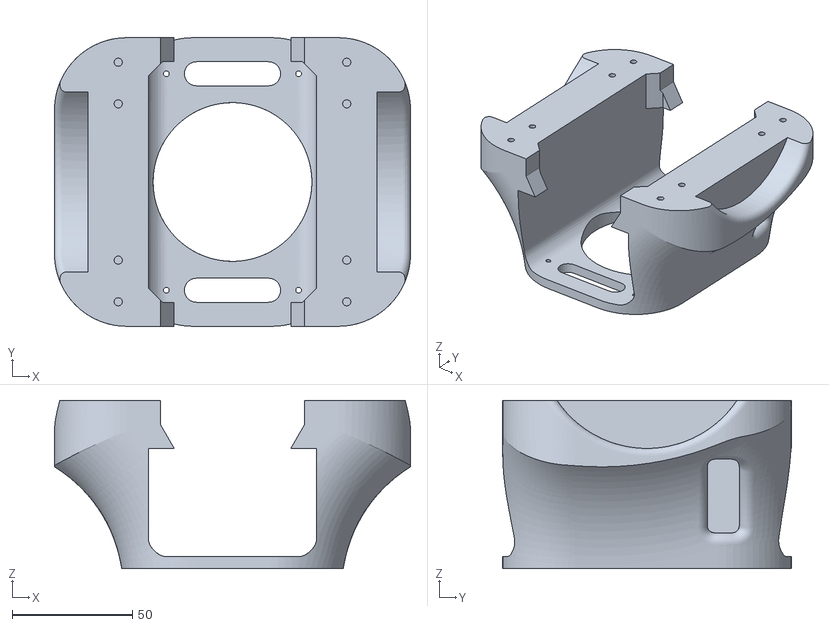
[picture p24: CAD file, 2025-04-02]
Hardware/CAD/Body.stl
148.0 x 120.0 x 70.0

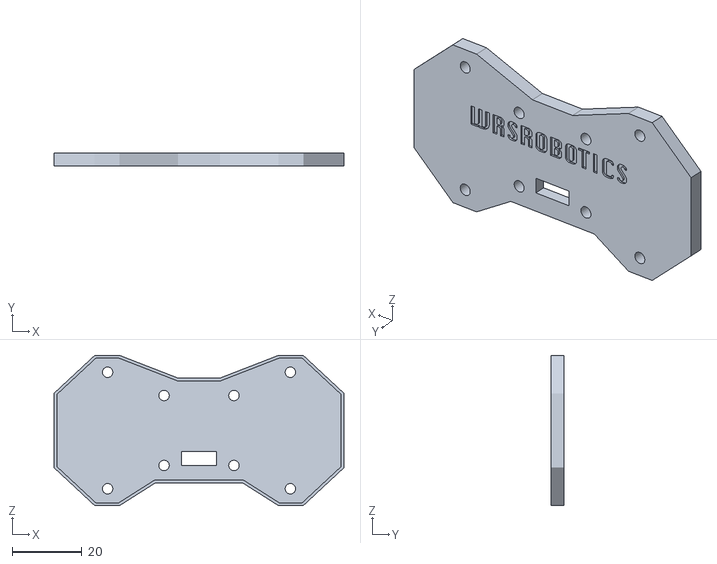
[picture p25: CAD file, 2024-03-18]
Hardware/CAD/Lid.stl
83.0 x 3.80 x 43.0

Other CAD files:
Matlab/CAD/WHEEL.stl
Matlab/CAD/top.stl
Hardware/CAD/BatteryPack v24.stl
Matlab/CAD/Body.stl
Matlab/CAD/BatteryPack v23.f3d
Matlab/CAD/ESP32-DEVKIT-V1.f3d

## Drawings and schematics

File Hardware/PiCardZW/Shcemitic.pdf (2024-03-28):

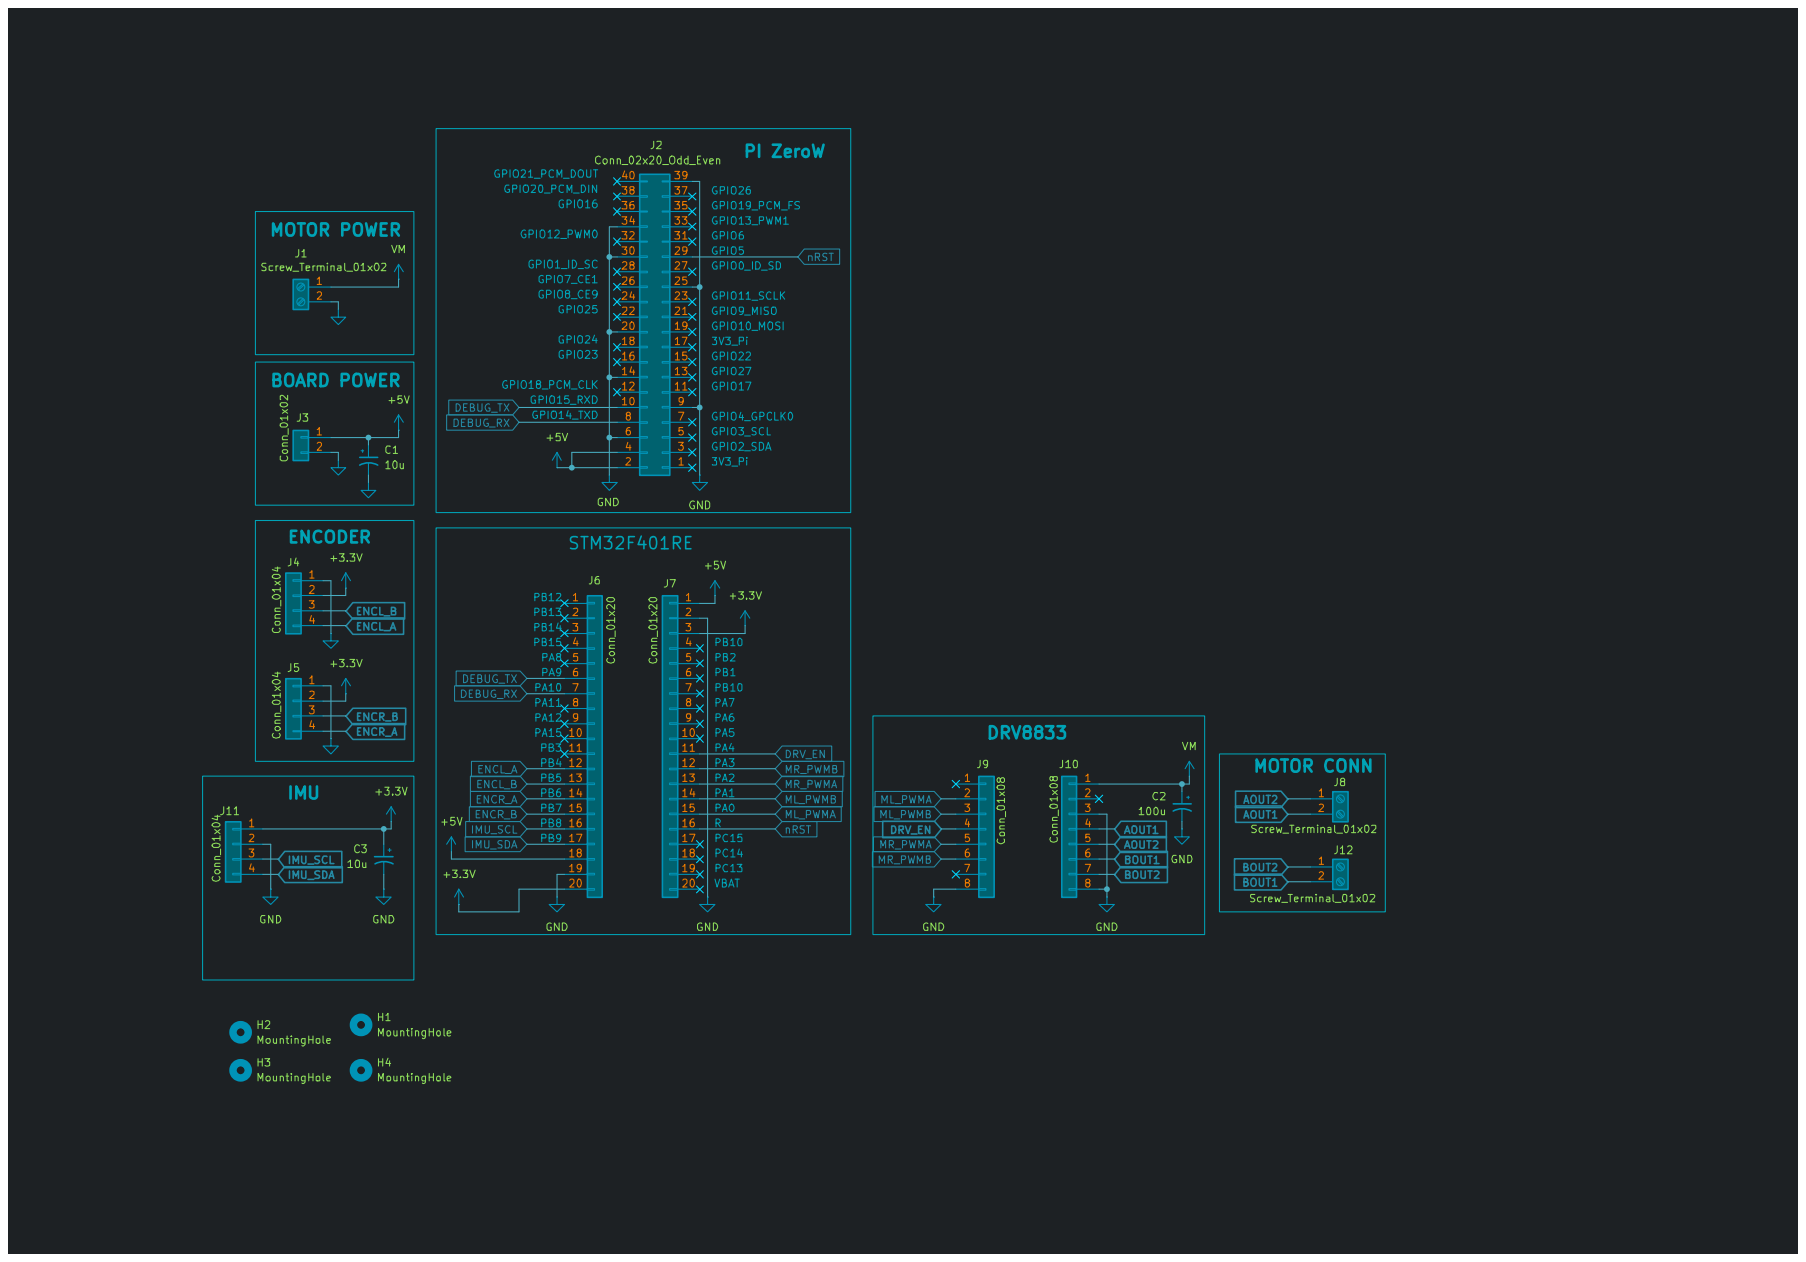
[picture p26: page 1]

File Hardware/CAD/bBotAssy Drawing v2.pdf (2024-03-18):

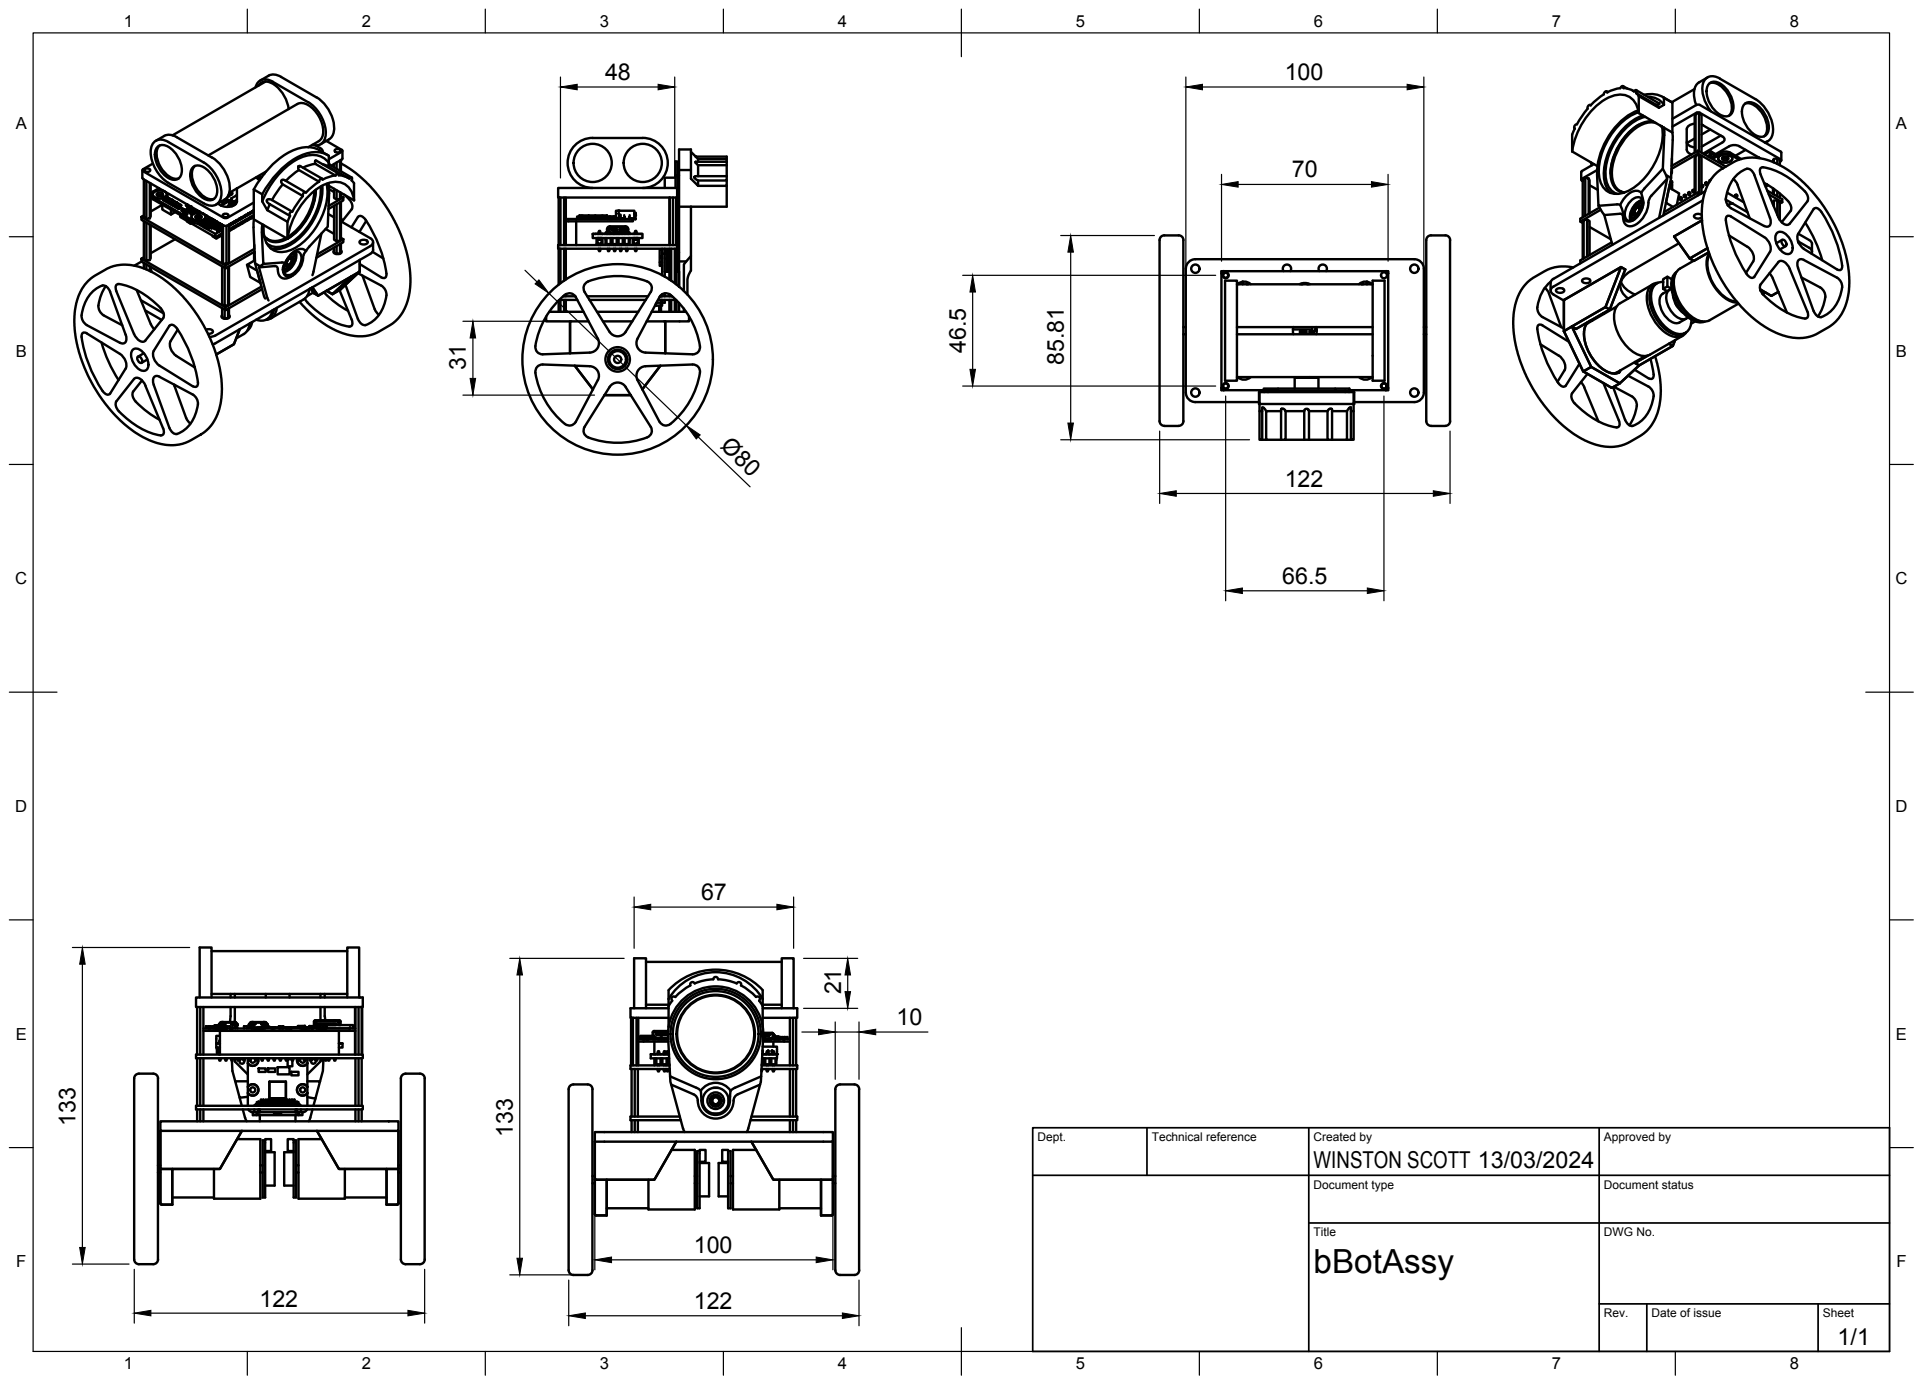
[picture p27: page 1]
Dept.; Technical reference; Created by; Approved by; Document type; Document status; Title; DWG No.; Rev.; Date of issue; Sheet; WINSTON SCOTT

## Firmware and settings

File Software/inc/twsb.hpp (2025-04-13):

#ifndef TWSB_H
#define TWSB_H

#include <termios.h>
#include <fcntl.h>
#include <queue>

#include "../common/common.hpp"
#include "../common/coms.hpp"

#define DEFAULT_PORT "/dev/ttyAMA0"
#define DEFAULT_BAUD 115200
#define SERCOMS_RX_BUFFER_SIZE 1024

#define NODE_NAME "TWSB"

//@Brief: Configure the serial port non-canonical mode
int config_serial_port(const std::string& port, int baud) {
    int serial_port_fd = open(port.c_str(), O_RDWR | O_NOCTTY | O_NONBLOCK); 
    if (serial_port_fd == -1) {
        std::cerr << "Error: Unable to open serial port " << port << std::endl;
        return -1;
    }
    struct termios options;
    tcgetattr(serial_port_fd, &options); // load current settings
    speed_t speed;
    switch (baud) {
        case 9600: speed = B9600; break;
        case 19200: speed = B19200; break;
        case 38400: speed = B38400; break;
        case 57600: speed = B57600; break;
        case 115200: speed = B115200; break;
        case 230400: speed = B230400; break;
        default: 
            close(serial_port_fd);
            throw std::runtime_error("Unsupported baud rate.");
    }
    cfsetispeed(&options, speed);
    cfsetospeed(&options, speed);
    options.c_cflag |= (CLOCAL | CREAD); 
    options.c_cflag &= ~PARENB; // No parity
    options.c_cflag &= ~CSTOPB; // 1 stop bit 
    options.c_cflag &= ~CSIZE; // Mask the character size bits
    options.c_oflag &= ~OPOST; // raw output
    options.c_iflag &= ~ICANON; // Non Canonical mode
    options.c_iflag &= ~ECHO;  // No echo
    options.c_iflag &= ~ECHOE; // No erasure
    options.c_iflag &= ~ISIG; // No interpretation of INTR, QUIT and SUSP
    options.c_cflag &= ~CRTSCTS;   // No flow control
    options.c_cflag |= CS8; // 8 data bits
    options.c_cc[VMIN] = 0; // Read doesn't block
    options.c_cc[VTIME] = 10; 

    if (tcsetattr(serial_port_fd, TCSANOW, &options) != 0) {
        close(serial_port_fd);
        std::cerr << "Error: Unable to configure serial port " << port << std::endl;
        return -1;
    }
    return serial_port_fd;
}

inline int get_bytes_available(int fd) {
    int num_bytes;
    ioctl(fd, FIONREAD, &num_bytes);
    return num_bytes;
}


// ----------------- PC SERIAL Implementation Pub-RPC Protocol ----------------- //
enum SERCOMS_DECODE_TELEM { COMS_TELEM_IDLE = 0, COMS_TELEM_ID, COMS_TELEM_DATA, COMS_TELEM_ERROR};
struct SerComs {
    Message _telem_msg_rx;
    std::queue<Message> telemMsgQ;
    SERCOMS_DECODE_TELEM telemDecodeState;
    std::vector<uint8_t> rxBuffer; // Now owned by SerComs

    // Constructor that initializes the vector with a given size.
    SerComs()
        : rxBuffer(SERCOMS_RX_BUFFER_SIZE) {
        telemDecodeState = COMS_TELEM_IDLE;
    }
};
//@Brief: Grab the ASCII message frame from the serial port read buffer
//@Description: Parses inplace teh xMacro string mapped to the decoded Publisher ID
//@Note: Multiple messages are pared and pushed to the message queue
//@Note: Partial Messages are completed and verified in the next read
void sercoms_grab_telemetry(int serialFd, struct SerComs& coms, struct Protocol& proto, 
                            PubMap& pub_map) {
    // read line from serial port until new line 
    int bytesAvailable = get_bytes_available(serialFd);
    bytesAvailable = std::min(bytesAvailable, static_cast<int>(coms.rxBuffer.size())); 
    ssize_t bytesRead = read(serialFd, coms.rxBuffer.data(), bytesAvailable);
    size_t idx = 0; // index into the buffer
    while ((bytesRead - static_cast<ssize_t>(idx)) > 0) {
        uint8_t byte = coms.rxBuffer[idx++];
        switch (coms.telemDecodeState) {
            case COMS_TELEM_IDLE:
                if (byte == proto.sof_byte) {
                    coms._telem_msg_rx.data.clear(); // Clear the data buffer for the new message
                    coms.telemDecodeState = COMS_TELEM_ID;
                }
                break;
            case COMS_TELEM_ID:
                byte = proto_decode_id(proto, byte);
                coms._telem_msg_rx.topic = pub_map.get_topic_name(byte);
                if(coms._telem_msg_rx.topic.empty()) {
                    coms.telemDecodeState = COMS_TELEM_ERROR;
                } else {
                    coms.telemDecodeState = COMS_TELEM_DATA;
                }
                break;
            case COMS_TELEM_DATA:
               if (byte == proto.eof_byte) { // End of Message
                    auto time = std::chrono::system_clock::now().time_since_epoch().count();
                    coms._telem_msg_rx.time_str = std::to_string(time);
                    coms.telemMsgQ.push(coms._telem_msg_rx);
                    coms.telemDecodeState = COMS_TELEM_IDLE;
                } else {
                    coms._telem_msg_rx.data.push_back(byte);
                }
                break;
            case COMS_TELEM_ERROR:
                coms.telemDecodeState = COMS_TELEM_IDLE;
                break;
            default:
                coms.telemDecodeState = COMS_TELEM_IDLE;
                break;
        }
    }
}

#endif // TWSB_H

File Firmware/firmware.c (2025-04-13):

// Motor Driver Firmware

#include "common/common.h"
#include "common/task.h"

#include "inc/MPU6050.h"

#include "inc/imu.h"
#include "inc/pid.h"
#include "inc/motor.h"
#include "inc/ddmr.h"
#include "inc/lqr.h"
#include "pubrpc/serComs.h" // Serial Communications to PC

// ********** GLOBAL STATIC BUFFERS ***************************************// ACCESS THROUGH RING BUFFER 
uint8_t rx1_buf_[512] = {0};
uint8_t tx1_buf_[2048] = {0};
float uuid = 3.14159;
// ********** CASCADED PID FUNCTIONS ***************************************//
//@Brief: Motor Speed Control Loop
static void runMotorSpeedLoop(struct Motor *m){
    m->speedCtrl.out = pidRun(&m->speedCtrl, m->wheelRPS);
    motorSetVoltage(m, m->speedCtrl.out);
}
//@Brief: Balance Angle Control Loop
static void runBalanceLoop(struct PID *balanceAngleCtrl, struct PID *steerCtrl, struct IMU *imu, 
                            struct Motor *motorL, struct Motor *motorR){
    // error = (Reference - Calibrated Offset) - Estimated Pitch
    balanceAngleCtrl->out = pidRun(balanceAngleCtrl, imu->kal.pitch); // Unicycle Wheel Speed output
    motorSetTrgtSpeed(motorL, (balanceAngleCtrl->out + steerCtrl->out)); // Apply Steering Correction
    motorSetTrgtSpeed(motorR, (balanceAngleCtrl->out - steerCtrl->out)); // Apply Steering Correction
}
//@Brief: Differential Drive Velocity Control Loop
static void runVelocityLoop(struct PID *velCtrl,struct PID *steerCtrl, struct PID *balanceAngleCtrl, 
                            struct DiffDriveModel *ddmr){          
    velCtrl->out = pidRun(velCtrl, ddmr->v_b); // Reference - odometry velocity 
    steerCtrl->out = pidRun(steerCtrl,ddmr->w_b); // Reference - odometry angular velocity
    pidSetRef(balanceAngleCtrl, -velCtrl->out); // Sets Balance Reference point to reach desired velocity
}
// ********** LQR FUNCTIONS ***************************************//
static void runLQR(struct LQR *lqr, struct Motor *motorL, struct Motor *motorR){
    float xpos = *lqr->state.x[0];
    float linVel = *lqr->state.x[1];
    float pitch = *lqr->state.x[2] * DEG_TO_RAD;
    float pitchRate = *lqr->state.x[3] * DEG_TO_RAD;
    
    lqr->u = -lqr->K[0] * xpos - lqr->K[1] * linVel - lqr->K[2] * pitch - lqr->K[3] * pitchRate;

    motorSetVoltage(motorL, lqr->u);
    motorSetVoltage(motorR, lqr->u);
}
// ********* SUPER LOOP **************** // 
int main(void){
    float nextMode = 0;
	// ***************************** HARDWARE SETUP ******************************************************** //
	systemClockSetup();      // Main System external XTAL 25MHz Init Peripheral Clocks
	systick_setup();    // 1ms Tick 
	struct GPIO led = initGPIO(GPIO13, GPIOC, GPIO_MODE_OUTPUT, GPIO_PUPD_NONE);
    struct GPIO drvMode = initGPIO(DRV_MODE_PIN, DRV_MODE_PORT, GPIO_MODE_OUTPUT, GPIO_PUPD_PULLDOWN); // Set DRV8876 Mode
    gpio_clear(drvMode.port, drvMode.pin); // Gnd == PWM Mode

    // Serial 
    struct Serial ser1 = serialInit( DEBUG_USART, DEBUG_PORT, DEBUG_RX, DEBUG_TX, GPIO_AF7, 
                            NVIC_USART1_IRQ, 
                            rx1_buf_, ARRAY_SIZE(rx1_buf_), 
                            tx1_buf_, ARRAY_SIZE(tx1_buf_));
    serialConfig(&ser1, 230400, 8, 1, USART_PARITY_NONE, USART_FLOWCONTROL_NONE);// Baud > 9*(PacketByteSize*rate)
    // IMU 
    i2cInit(IMU_PERIF, IMU_PORT, IMU_SCL, IMU_SDA);
    struct MPU6050 mpu6050 = mpu6050Init(IMU_PERIF);
    struct IMU imu = imuInit(IMU_A_ACCEL, IMU_A_GYRO,IMU_A_COMP, (IMU_PERIOD * MS_TO_S));
    imuLinkSensor(&imu, &mpu6050);
    // MOTORS 
    struct Encoder encL = encoderInit(ENC_L_TIM, UINT16_MAX, ENC_L_B, ENC_L_PORT, ENC_L_A, ENC_L_PORT, ENC_L_AF, true);
    struct Encoder encR = encoderInit(ENC_R_TIM, UINT16_MAX, ENC_R_B, ENC_R_PORT, ENC_R_A, ENC_R_PORT, ENC_R_AF, false);
    struct Motor motorL = motorInit(M_L_TIM, M_L_PORT, TIM_OC1, M_L_PWMA, TIM_OC2, M_L_PWMB, DRV_EN_PIN, DRV_EN_PORT);
    struct Motor motorR = motorInit(M_R_TIM, M_R_PORT, TIM_OC3, M_R_PWMA, TIM_OC4, M_R_PWMB, DRV_EN_PIN, DRV_EN_PORT);
    motorDisable(&motorL); // Ensure Driver is Disabled Before Configuration
    motorDisable(&motorR); //
    motorConfig(&motorL, &encL, VSYS, MOTOR_DEADBAND,VMOTOR_MAX, true, SPEED_ALPHA, RPS_MAX);
    motorConfig(&motorR, &encR, VSYS, MOTOR_DEADBAND,VMOTOR_MAX, false,  SPEED_ALPHA, RPS_MAX );

    // BALANCE CONTROLLER
    struct PID balanceAngleCtrl = pidInit(-RPS_MAX, RPS_MAX, BAL_KP, BAL_KI, BAL_KD, (BAL_CNTRL_PERIOD * MS_TO_S));
    pidSetRef(&balanceAngleCtrl, -7.5f);
    // DIFFERENTIAL DRIVE MODEL (LinVel, AngVel)
    struct DiffDriveModel ddmr = ddmrInit(WHEEL_RADIUS, WHEEL_BASE, VEL_ALPHA, STEER_ALPHA, ODOM_PERIOD * MS_TO_S);
    struct PID velCtrl = pidInit(-3, 3, VEL_P, VEL_I, VEL_D, (VEL_CNTRL_PERIOD * MS_TO_S));   
    struct PID steerCtrl = pidInit(-5,5, STEER_KP, STEER_KI, STEER_KD, VEL_CNTRL_PERIOD * MS_TO_S);
    // LQR Controller
    struct LQR lqr ={.K[0] = LQR_K1, .K[1] = LQR_K2, .K[2] = LQR_K3, .K[3] = LQR_K4, 
        .state.x = {&ddmr.posX, &ddmr.v_b, &imu.kal.pitch, &imu.kal.pitchRate}};

    // ***************************** COMMUNICATIONS ******************************************************** // 
    struct Coms coms = comsInit();
    // -------------------- TOPIC PUBLISHERS ---------------------- //
    comsRegisterPub(&coms, PUB_CMD_RET, SERIALIZED_CMDRET_FTM);
    comsRegisterPub(&coms, PUB_ERROR,   SERIALIZED_ERROR_FMT);
    comsRegisterPub(&coms, PUB_INFO,    SERIALIZED_INFO_FMT);
    comsRegisterPub(&coms, PUB_DEBUG,   SERIALIZED_DEBUG_FMT);
    comsRegisterPub(&coms, PUB_TELEM,   SERIALIZED_TELEM_FMT);
    // --------------------PARAMETER REGISTERS ---------------------- //
    comsRegisterParam(&coms, P_ID,      "%f", &uuid);
    comsRegisterParam(&coms, P_MODE,    "%f", &nextMode);
    // - LEFT MOTOR
    comsRegisterParam(&coms, P_LTRGT,   "%f", &motorL.speedCtrl.ref);
    comsRegisterParam(&coms, P_LKP,     "%f", &motorL.speedCtrl.kp);
    comsRegisterParam(&coms, P_LKI,     "%f", &motorL.speedCtrl.ki);
    // - RIGHT MOTOR
    comsRegisterParam(&coms, P_RTRGT,   "%f", &motorR.speedCtrl.ref);
    comsRegisterParam(&coms, P_RKP,     "%f", &motorR.speedCtrl.kp);
    comsRegisterParam(&coms, P_RKI,     "%f", &motorR.speedCtrl.ki);
    // - BALANCE CONTROLLER
    comsRegisterParam(&coms, P_BTRGT,   "%f", &balanceAngleCtrl.ref);
    comsRegisterParam(&coms, P_BKP,     "%f", &balanceAngleCtrl.kp);
    comsRegisterParam(&coms, P_BKI,     "%f", &balanceAngleCtrl.ki);
    comsRegisterParam(&coms, P_BKD,     "%f", &balanceAngleCtrl.kd);
    // - Linear Velocity Controller
    comsRegisterParam(&coms, P_VTRGT,   "%f", &velCtrl.ref);
    comsRegisterParam(&coms, P_VKP,     "%f", &velCtrl.kp);
    comsRegisterParam(&coms, P_VKI,     "%f", &velCtrl.ki);
    comsRegisterParam(&coms, P_VKD,     "%f", &velCtrl.kd);
    comsRegisterParam(&coms, P_VAPLHA,  "%f", &ddmr.linearVelAlpha);
    // - Angular Velocity Controller
    comsRegisterParam(&coms, P_ATRGT,   "%f", &steerCtrl.ref);
    comsRegisterParam(&coms, P_AKP,     "%f", &steerCtrl.kp);
    comsRegisterParam(&coms, P_AKI,     "%f", &steerCtrl.ki);
    comsRegisterParam(&coms, P_AKD,     "%f", &steerCtrl.kd);
    comsRegisterParam(&coms, P_AALPHA,  "%f", &ddmr.angularVelAlpha);
    // - IMU Parameters
    comsRegisterParam(&coms, P_IMU_AA,  "%f", &imu.lpf.alpha_accel);
    comsRegisterParam(&coms, P_IMU_GA,  "%f", &imu.lpf.alpha_gyro);
    comsRegisterParam(&coms, P_IMU_KQ,  "%f", &imu.kal.pitchK.Q_angle);
    comsRegisterParam(&coms, P_IMU_KQB, "%f", &imu.kal.pitchK.Q_bias);
    comsRegisterParam(&coms, P_IMU_KR,  "%f", &imu.kal.pitchK.R_measure);
    comsRegisterParam(&coms, P_IMU_A_XOFFSET,  "%f", &imu.sensor->offset.accel.x);
    comsRegisterParam(&coms, P_IMU_A_YOFFSET, "%f", &imu.sensor->offset.accel.y);
    comsRegisterParam(&coms, P_IMU_A_ZOFFSET, "%f", &imu.sensor->offset.accel.z);
    comsRegisterParam(&coms, P_IMU_MOUNT_OFFSET, "%f", &imu.sensor->mount_offset);
    comsRegisterParam(&coms, P_K1, "%f", &lqr.K[0]);
    comsRegisterParam(&coms, P_K2, "%f", &lqr.K[1]);
    comsRegisterParam(&coms, P_K3, "%f", &lqr.K[2]);
    comsRegisterParam(&coms, P_K4, "%f", &lqr.K[3]);

    // ************************************************************** //
    comsSendMsg(&coms, &ser1, PUB_INFO, "POST PASSED");
    // ***** Application Tasks **************************************************************************** // 
    struct FixedTimeTask blinkTask = createTask(BLINK_PERIOD);      // Watchdog led
    struct FixedTimeTask comsCmdTask = createTask(COMSCMD_PERIOD); // SUB RPC 
    struct FixedTimeTask comsPUBTask = createTask(COMSPUB_PERIOD); // PUB Telemetry
    struct FixedTimeTask imuTask =  createTask(IMU_PERIOD); // IMU Read
    struct FixedTimeTask odomTask =  createTask(ODOM_PERIOD); // Odometry
    struct FixedTimeTask wspeedCntlTask = createTask(WSPEED_CNTRL_PERIOD); // Motor Speed Control
    struct FixedTimeTask balanceCntrlTask = createTask(BAL_CNTRL_PERIOD);  // Balance Control Loop
    struct FixedTimeTask velCtrlTask = createTask(VEL_CNTRL_PERIOD);  // Velocity Control Loop
    struct FixedTimeTask lqrTask = createTask(LQR_CNTRL_PERIOD); // LQR Controller


    // ****** Loop Parameters **************************************************************************** // 
    enum MODE {FW_UPDATE=0,INIT,PARK, CASCADE, LQR,  TUNE_MOTOR, COMMISSION, SYSID} mode;
    nextMode = INIT;
    motorEnable(&motorL);
    motorEnable(&motorR);

    uint16_t loopTick = 0;
	for(;;){
        loopTick = sysGetMillis(); // Update Loop Time
        mode = nextMode;
        switch (mode){
            case FW_UPDATE:
                comsSendMsg(&coms, &ser1, PUB_INFO, "FW_UPDATE");
                // Disable Motors, safety disable drivers
                motorDisable(&motorL);
                motorDisable(&motorR);
                // Set GPIO Values High Z
                gpio_mode_setup(GPIOA, GPIO_MODE_INPUT, GPIO_PUPD_NONE, GPIO_ALL);
                gpio_mode_setup(GPIOB, GPIO_MODE_INPUT, GPIO_PUPD_NONE, GPIO_ALL);
                gpio_mode_setup(GPIOC, GPIO_MODE_INPUT, GPIO_PUPD_NONE, GPIO_ALL);
                // Jump to Bootloader
                systemReflash();
                break;
            case INIT: // Initialize System 
                // State Transition
                if(sysGetMillis() >= 3000){ // 3s Startup helps stabilize Kalman Filter
                    systick_clear();
                    pidClear(&velCtrl);
                    pidClear(&balanceAngleCtrl);
                    pidClear(&steerCtrl);
                    motorDisable(&motorL);
                    motorDisable(&motorR);
                    motorStop(&motorL);
                    motorStop(&motorR); 
                    nextMode = PARK;
                    comsSendMsg(&coms, &ser1, PUB_INFO, "INIT => PARK ");
                }
                break;
            case PARK:
                // State Transition
                if(_fabs(imu.kal.pitch) <= BAL_CUTOFF){ // Safety Cut Off
                    motorEnable(&motorL);
                    motorEnable(&motorR);
                    pidClear(&velCtrl);
                    pidClear(&balanceAngleCtrl);
                    pidClear(&steerCtrl);
                    ddmrReset(&ddmr);
                    nextMode = CASCADE;
                    comsSendMsg(&coms, &ser1, PUB_INFO, "PARK => RUN");
                }
                break;
            case CASCADE:
                if(_fabs(imu.kal.pitch) >= BAL_CUTOFF){  // Safety Cut Off
                    motorDisable(&motorL);
                    motorDisable(&motorR);
                    nextMode = PARK;
                    comsSendMsg(&coms, &ser1, PUB_INFO, "CASCADE => PARK "); 
                    break;
                }
                if(CHECK_PERIOD(wspeedCntlTask, loopTick)){
                    runMotorSpeedLoop(&motorL);
                    runMotorSpeedLoop(&motorR);
                    wspeedCntlTask.lastTick = loopTick;
                }
                if(CHECK_PERIOD(balanceCntrlTask, loopTick)){  
                    runBalanceLoop(&balanceAngleCtrl, &steerCtrl, &imu, &motorL, &motorR);
                    balanceCntrlTask.lastTick = loopTick;
                }
                if(CHECK_PERIOD(velCtrlTask, loopTick)){    
                    runVelocityLoop(&velCtrl, &steerCtrl, &balanceAngleCtrl, &ddmr);
                    velCtrlTask.lastTick= loopTick;
                }
                break;
            case LQR:
                if(_fabs(imu.kal.pitch) >= BAL_CUTOFF){  // Safety Cut Off
                    motorDisable(&motorL);
                    motorDisable(&motorR);
                    nextMode = PARK;
                    comsSendMsg(&coms, &ser1, PUB_INFO, "LQR => PARK "); 
                    break;
                }
                if(CHECK_PERIOD(lqrTask, loopTick)){
                    runLQR(&lqr, &motorL, &motorR);
                    lqrTask.lastTick = loopTick;
                }
                break;
            case TUNE_MOTOR:
                motorEnable(&motorL);
                motorEnable(&motorR);
                nextMode = COMMISSION;
                comsSendMsg(&coms, &ser1, PUB_INFO, "TUNE_MOTOR => COMMISSION");
                break;
            case COMMISSION:
                if(CHECK_PERIOD(wspeedCntlTask, loopTick)){
                    runMotorSpeedLoop(&motorL);
                    runMotorSpeedLoop(&motorR);
                    wspeedCntlTask.lastTick = loopTick;
                }
                break;
            case SYSID:
                if(CHECK_PERIOD(wspeedCntlTask, loopTick)){
                    motorSetVoltage(&motorL, motorL.speedCtrl.ref);
                    motorSetVoltage(&motorR, motorR.speedCtrl.ref);
                    wspeedCntlTask.lastTick = loopTick;
                }
                break;
            default:
                nextMode = PARK;
                break;   
        };

        // ********** ODOMETRY ********************************************************************************* //
        if(CHECK_PERIOD(odomTask, loopTick)){
            motorEstSpeed(&motorL);
            motorEstSpeed(&motorR);
            ddmrEstimateOdom(&ddmr, &motorL, &motorR);
            odomTask.lastTick = loopTick;
        }
        // ********** IMU ********************************************************************************* //
        if(CHECK_PERIOD(imuTask, loopTick)){
            mpu6050Read(&mpu6050);
            imuLPF(&imu, &mpu6050.accel, &mpu6050.gyro);
            imuKalUpdate(&imu);
            imu.kal.pitch += imu.sensor->mount_offset;
            imuTask.lastTick = loopTick;
        }
        // ********** Communications ********************************************************************** //
        if(CHECK_PERIOD(comsCmdTask, loopTick)){
            // Handle RX Messages 
            while(rbEmpty(&ser1.rxRB)==false){
                if(comsGrabCmdMsg(&coms, &ser1)){
                    comsExecuteRPC(&coms, &ser1);
                }
            }
            comsCmdTask.lastTick = loopTick;
        }
        if(CHECK_PERIOD(comsPUBTask, loopTick)){
            // TX Publishing Telemetry
            comsSendMsg(&coms, &ser1, PUB_TELEM,    
                imu.kal.pitch,      imu.kal.roll, 
                imu.lpf.accel.x,    imu.lpf.accel.y,        imu.lpf.accel.z,
                imu.lpf.gyro.x,     imu.lpf.gyro.y,         imu.lpf.gyro.z,
                motorL.wheelRPS,    motorL.speedCtrl.ref,   motorL.speedCtrl.out,
                motorR.wheelRPS,    motorR.speedCtrl.ref,   motorR.speedCtrl.out,
                ddmr.v_b,           velCtrl.ref,            balanceAngleCtrl.ref, 
                ddmr.w_b,           steerCtrl.ref,          steerCtrl.out,
                ddmr.posX,          ddmr.x_g,               ddmr.y_g,
                ddmr.psi,           lqr.u);

            comsPUBTask.lastTick = loopTick;
        }

        // ********* DEBUG LED ******************************************************************* // 
        if(CHECK_PERIOD(blinkTask, loopTick)){
            gpio_toggle(led.port, led.pin);
            blinkTask.lastTick = loopTick;  
        }
    }
}

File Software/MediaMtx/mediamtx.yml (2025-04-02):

###############################################
# Global settings

# Settings in this section are applied anywhere.

###############################################
# Global settings -> General

# Verbosity of the program; available values are "error", "warn", "info", "debug".
logLevel: info
# Destinations of log messages; available values are "stdout", "file" and "syslog".
logDestinations: [stdout]
# If "file" is in logDestinations, this is the file which will receive the logs.
logFile: mediamtx.log

# Timeout of read operations.
readTimeout: 10s
# Timeout of write operations.
writeTimeout: 10s
# Size of the queue of outgoing packets.
# A higher value allows to increase throughput, a lower value allows to save RAM.
writeQueueSize: 512
# Maximum size of outgoing UDP packets.
# This can be decreased to avoid fragmentation on networks with a low UDP MTU.
udpMaxPayloadSize: 1472

# Command to run when a client connects to the server.
# This is terminated with SIGINT when a client disconnects from the server.
# The following environment variables are available:
# * MTX_CONN_TYPE: connection type
# * MTX_CONN_ID: connection ID
# * RTSP_PORT: RTSP server port
runOnConnect:
# Restart the command if it exits.
runOnConnectRestart: no
# Command to run when a client disconnects from the server.
# Environment variables are the same of runOnConnect.
runOnDisconnect:

###############################################
# Global settings -> Authentication

# Authentication method. Available values are:
# * internal: users are stored in the configuration file
# * http: an external HTTP URL is contacted to perform authentication
# * jwt: an external identity server provides authentication through JWTs
authMethod: internal

# Internal authentication.
# list of users.
authInternalUsers:
  # Default unprivileged user.
  # Username. 'any' means any user, including anonymous ones.
- user: any
  # Password. Not used in case of 'any' user.
  pass:
  # IPs or networks allowed to use this user. An empty list means any IP.
  ips: []
  # List of permissions.
  permissions:
    # Available actions are: publish, read, playback, api, metrics, pprof.
  - action: publish
    # Paths can be set to further restrict access to a specific path.
    # An empty path means any path.
    # Regular expressions can be used by using a tilde as prefix.
    path:
  - action: read
    path:
  - action: playback
    path:

  # Default administrator.
  # This allows to use API, metrics and PPROF without authentication,
  # if the IP is localhost.
- user: any
  pass:
  ips: ['127.0.0.1', '::1']
  permissions:
  - action: api
  - action: metrics
  - action: pprof

# HTTP-based authentication.
# URL called to perform authentication. Every time a user wants
# to authenticate, the server calls this URL with the POST method
# and a body containing:
# {
#   "user": "user",
#   "password": "password",
#   "ip": "ip",
#   "action": "publish|read|playback|api|metrics|pprof",
#   "path": "path",
#   "protocol": "rtsp|rtmp|hls|webrtc|srt",
#   "id": "id",
#   "query": "query"
# }
# If the response code is 20x, authentication is accepted, otherwise
# it is discarded.
authHTTPAddress:
# Actions to exclude from HTTP-based authentication.
# Format is the same as the one of user permissions.
authHTTPExclude:
- action: api
- action: metrics
- action: pprof

# JWT-based authentication.
# Users have to login through an external identity server and obtain a JWT.
# This JWT must contain the claim "mediamtx_permissions" with permissions,
# for instance:
# {
#  ...
#  "mediamtx_permissions": [
#     {
#       "action": "publish",
#       "path": "somepath"
#     }
#   ]
# }
# Users are expected to pass the JWT in the Authorization header or as a query parameter.
# This is the JWKS URL that will be used to pull (once) the public key that allows
# to validate JWTs.
authJWTJWKS:
# name of the claim that contains permissions.
authJWTClaimKey: mediamtx_permissions

###############################################
# Global settings -> Control API

# Enable controlling the server through the Control API.
api: no
# Address of the Control API listener.
apiAddress: :9997
# Enable TLS/HTTPS on the Control API server.
apiEncryption: no
# Path to the server key. This is needed only when encryption is yes.
# This can be generated with:
# openssl genrsa -out server.key 2048
# openssl req -new -x509 -sha256 -key server.key -out server.crt -days 3650
apiServerKey: server.key
# Path to the server certificate.
apiServerCert: server.crt
# Value of the Access-Control-Allow-Origin header provided in every HTTP response.
apiAllowOrigin: '*'
# List of IPs or CIDRs of proxies placed before the HTTP server.
# If the server receives a request from one of these entries, IP in logs
# will be taken from the X-Forwarded-For header.
apiTrustedProxies: []

###############################################
# Global settings -> Metrics
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

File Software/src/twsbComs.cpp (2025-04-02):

/************************************************************************************
 *  @file    twsbComs.cpp
 *  @brief   Implementation of pub-rpc protocol for the TWSB over ZMQ
 *  Single-threaded Event Driven IO loop
 *  Parses in-place the xMacro string mapped to the decoded Publisher ID
 *  Bridges commands send over the ZMQ IPC socket to the TWSB over UART
 *  Provides raw command and topic subscription console to the serial port for debugging
 *  Publishes Timestamped Serialized Telemetry Messages to the ZMQ IPC socket
 * 
 *          ----> | ZMQ SUB | ----> | TWSB UART WRITE | ----> | TWSB |
 *          <---- | ZMQ PUB | <---- | TWSB UART READ  | <---- | TWSB |
 ************************************************************************************/
 
#include "../inc/twsb.hpp"

// ********* MAIN ************************************************************************* //
int main(int argc, char *argv[]) {
    // --------------- CLI Parsing ----------------- //
    if (argc < 3) {
        syslog(LOG_ERR, "Usage: %s <serial_port> <baud_rate>\n", argv[0]);
        return 1;
    }
    std::string port = argv[1];
    int baud_rate = std::stoi(argv[2]);
    if (port.empty() || baud_rate == 0) {
        syslog(LOG_ERR, "Error: Invalid Serial Port or Baud Rate\n");
        return 1;
    }

    // ---------- Communication Setup -------------- //
    Protocol proto = {.sof_byte = '<', .eof_byte = '\n', .delim_byte = ':', .offset = 'A'};
    CommandMsg cmd; // Working command variable
    PubMap pub_map("/home/pi/prog/software/configs/robotConfig.json", NODE_NAME); 
    struct SerComs coms;
    /* Note this Node is a transparent bridge between the ZMQ and the TWSB
    // All Parameters and Publishers are of the TWSB MCU as implemented in the Firmware
    // The Config is just loaded to provide a means of maping the publisher id to the
    // sting name as required by the ZMQ IPC message */
    
    // --------------- IO Setup ----------------- //
    syslog(LOG_INFO, "Configuring serial port %s at %d baud", port.c_str(), baud_rate);
    int serial_fd = config_serial_port(port, baud_rate);
    if (serial_fd == -1) {
        syslog(LOG_CRIT, "Error: Unable to open serial port %s\n", port.c_str());
        return 1;
    }

    // --------------- ZMQ Setup ----------------- //
    zmq::context_t context(1);
    // External Interface
    zmq::socket_t excmd_subsock(context, zmq::socket_type::sub); 
    excmd_subsock.set(zmq::sockopt::linger, 0);
    excmd_subsock.set(zmq::sockopt::subscribe, "");
    excmd_subsock.bind("tcp://*:5556"); // remote command server
    zmq::socket_t exmsg_pubsock(context, zmq::socket_type::pub);
    exmsg_pubsock.set(zmq::sockopt::linger, 0);
    exmsg_pubsock.bind("tcp://*:5555");  // message server   
    // Internal Interface to robot services  acts as a proxy to the external interface
    zmq::socket_t botcmd_pubsock(context, zmq::socket_type::pub);
    botcmd_pubsock.set(zmq::sockopt::linger, 0);
    botcmd_pubsock.bind("ipc:///tmp/botcmds"); // local command server 
    zmq::socket_t botmsg_subsock(context, zmq::socket_type::sub);
    botmsg_subsock.set(zmq::sockopt::linger, 0);
    botmsg_subsock.connect("ipc:///tmp/botmsgs");  // local telemetry server
    botmsg_subsock.set(zmq::sockopt::subscribe, ""); 
    // Ugly Arch but it works to patch cmds form other services round robin
    zmq::socket_t mcucmd_subsock(context, zmq::socket_type::sub); // 
    mcucmd_subsock.set(zmq::sockopt::linger, 0);
    mcucmd_subsock.connect("ipc:///tmp/vizcmds");
    mcucmd_subsock.connect("ipc:///tmp/joycmds");
    mcucmd_subsock.set(zmq::sockopt::subscribe, "TWSB"); // Subscribe to all topics

    // --------------- Console Setup ----------------- //
    zmq::pollitem_t poll_items[] = {
        { nullptr, serial_fd, ZMQ_POLLIN, 0 },                  // Bridge Serial Port to ZMQ
        {static_cast<void*>(excmd_subsock), 0, ZMQ_POLLIN, 0 }, // TWSB Receives Commands from PC 
        {static_cast<void*>(botmsg_subsock), 0, ZMQ_POLLIN, 0}, // Forward Telemetry to PC
        {static_cast<void*>(mcucmd_subsock), 0, ZMQ_POLLIN, 0}  // Forward Commands to MCU
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

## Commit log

2023-11-02 uart TX IRQ
2023-11-02 timer PWM
2023-11-02 I2C Sensor test
2023-11-02 MPU6050 MADJWICK FILTER
2023-11-05 Model Assembled
2023-11-05 V1 STL
    [BatteryPack.stl, Body.stl, Chassis Low.stl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]
2023-11-06 DC Driver SCH
    [DCMotorDriver.kicad_sch]
2023-11-06 layout v1
    [DCMotorDriver.kicad_pcb, DCMotorDriver.kicad_sch]
2023-11-15 tempFix IMU iniAddr
2023-12-29 IMU Quaternion-Euler
2024-02-27 imu LowPass
2024-03-12 DC Motor PI
2024-03-18 pubMsg & motorCleanup
2024-04-04 fix motor bug
2024-12-12 Software Structure
    [devicePub.csv, paramRegMap.csv, rawIMU.csv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]
